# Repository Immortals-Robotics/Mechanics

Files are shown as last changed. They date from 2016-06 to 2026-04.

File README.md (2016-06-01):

# Immortals Mechanics
The mechanical design of robots has no major change since 2012 and just some part of kicking system and dribbling system optimized for better performance.
The main chassis consists of a **5mm hard anodized 7075 aluminum alloy** plate on which motors, batteries, encoders, capacitors, and kicker systems are mounted. Robots are covered by a **carbon-fiber compound** that is light as it is solid.
In order to mechanically stabilize the robot movement and kicking, the altitude of the center of mass is lowered by arranging rather heavy parts on the plate, that level first in the whole robot structure.
The overall height of the robot is **148mm** and its diameter is **178mm**.
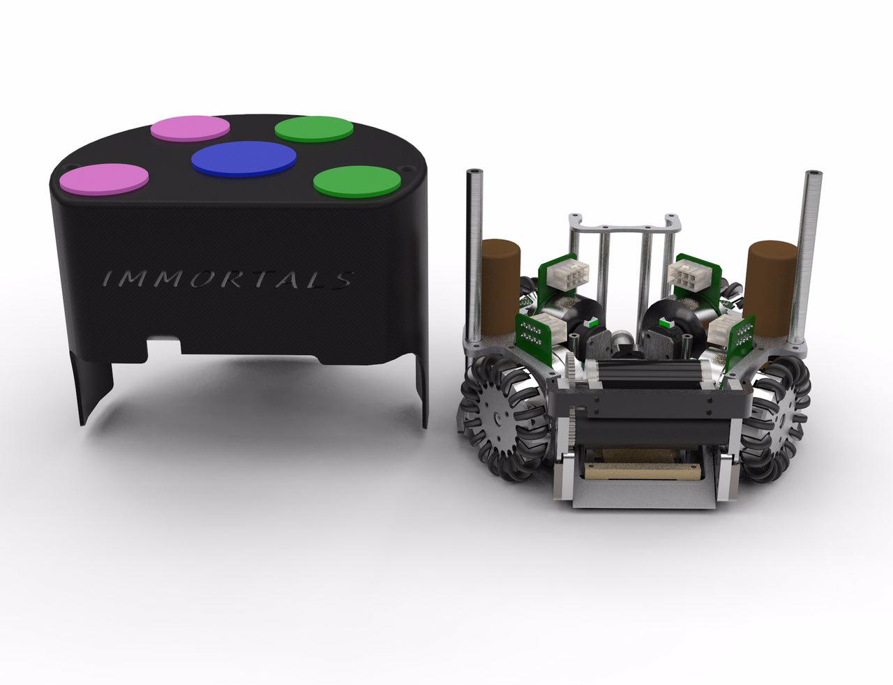
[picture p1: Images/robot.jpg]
Robot
 

## Wheels 
Robots are designed omni-directional by using **four** omni-wheels. Each wheel is **61mm** in diameters and has **18** rollers covered by double seal O-rings for better grip. Both wheels and rollers are made of **7075 aluminum alloy**. 
As the field size has been increased, higher speeds are inevitable; so the gear ratio is optimized to **45:12** and **50 Watts Maxon EC-45 brushless** motors are used to overcome the max-speed/max-acceleration trade off. The gearbox is merged into wheels to minimize the volume occupied by driving system. Its design is unique so that the gear used for transition is carved into the wheel itself.
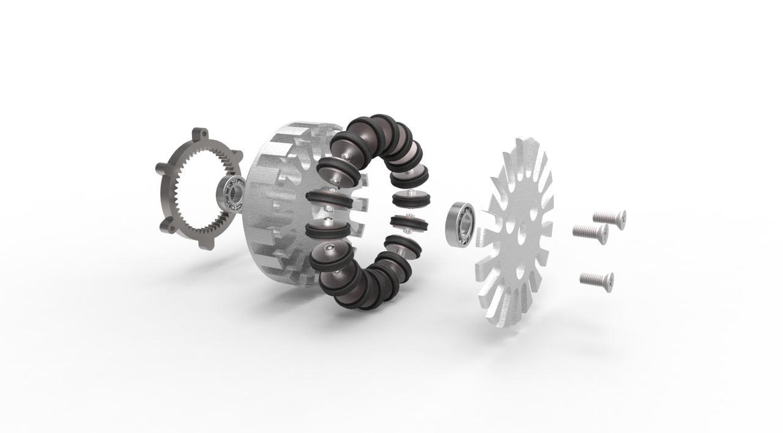
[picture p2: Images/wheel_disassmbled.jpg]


One of the major issues in the robots was inaccurate low-level navigation. After many experiments, measurements and inspections on the control system, it came out that non-identical mechanical properties of each gear are the biggest issue, which was caused by manufacturing inaccuracies. To have smoother and more accurate movement, gear module is redesigned with smaller module size this year. Also there are a little change in sub wheels design and tolerance to reduce unsteadiness and to stick better to the field during fast accelerations.   
## Casing
Although safe navigation has been a must for years in the league, highly dynamic nature of the SSL causes unavoidable collisions that lead to damages ranging from minor to severe. To avoid damages to internal parts, especially electronics which are fragile, making a robust, solid casing that can efficiently damp impacts is a necessity. Thus, a case made up of **2mm thick carbon-fiber compound** is made which is as solid as it is light to cover the whole body but kicking devices and the dribbler.

## Kicking & Dribbling System
To account for the increase in field size, the kicking system is redesigned and to have more power and accuracy in booth chip and direct shoots. Also because of some high voltage short circuit caused by magnet solenoids, in our new version whole kick system is isolated from body and there isn't any direct metal to metal contact by using resin as an isolator material. 
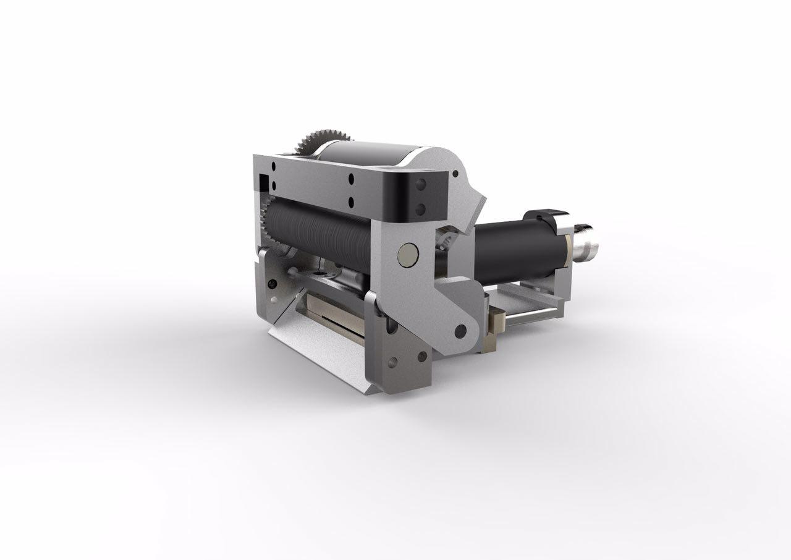
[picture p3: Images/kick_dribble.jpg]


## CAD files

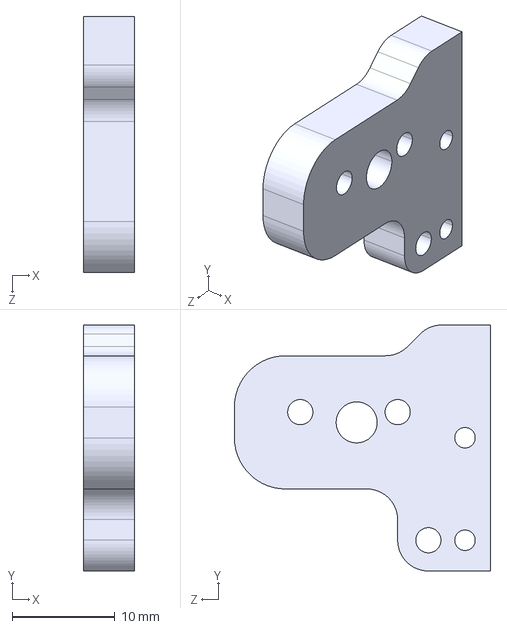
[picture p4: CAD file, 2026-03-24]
Manufacturing/Step/main holder (2 times).STEP
5.00 x 24.0 x 25.0 mm

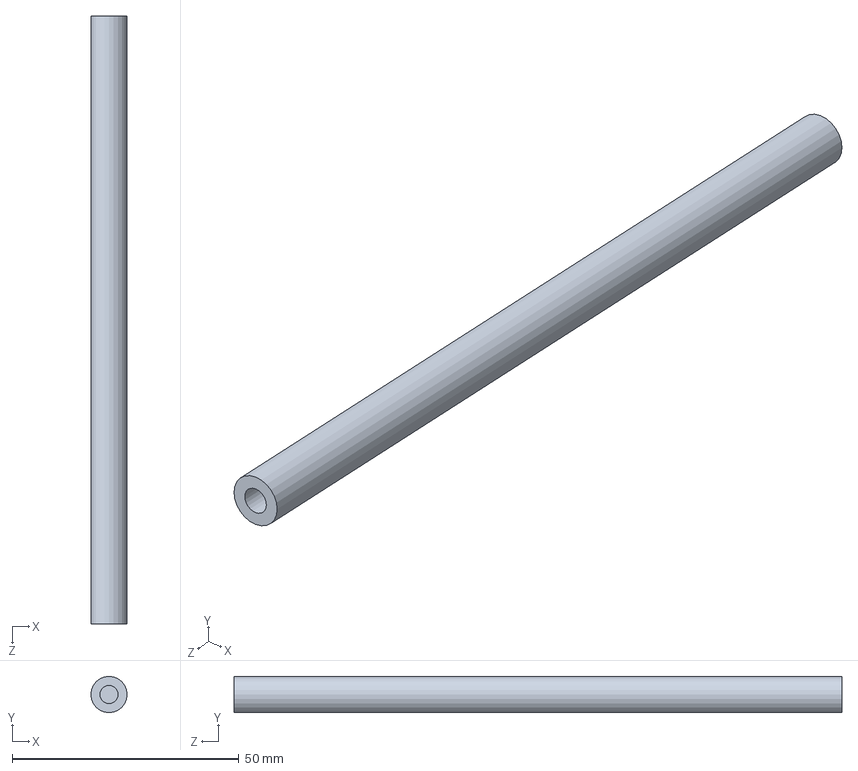
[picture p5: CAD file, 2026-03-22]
Spacer main.SLDPRT
8.00 x 8.00 x 134.0 mm

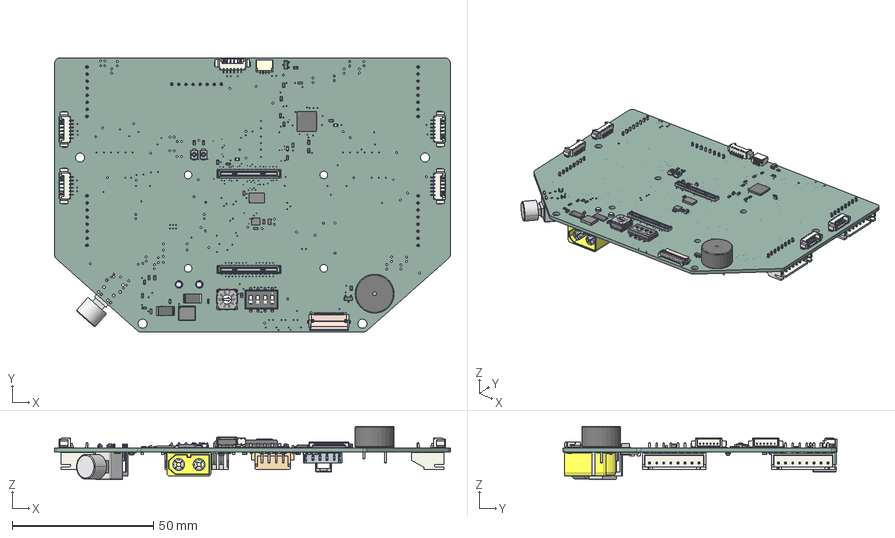
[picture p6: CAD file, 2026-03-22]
elec/main-board.step
140.0 x 97.0 x 18.9 mm
R_0603_1608Metric x 38
SOT-23 x 2
Indicator_PUI_AI-1440-TWT-24V-2-R
C_0603_1608Metric x 26
Molex_PicoBlade_53261-0671_1x06-1MP_P1.25mm_Horizontal x 5
FH12-22S-0.5SH_Èª
LED_0603_1608Metric x 3
ICM-42688-P
C_0805_2012Metric x 12
SW_DIP_SPSTx04_Slide_6.7x11.72mm_W8.61mm_P2.54mm_LowProfile
R_2512_6332Metric x 3
DHVQFN24
SW_SPST_B3U-1000P x 2
DF40C-100DS x 2
QFN-56-1EP_7x7mm_P0.4mm_EP3.2x3.2mm
BSC007N04LS6ATMA1
Nidec_Copal_SH-7010A
SH-700-Without knob (Minus slot)
SH-7050A_body
SM04B-SRSS-TB(LF)(SN)--3DModel-STEP-56544
JST_XH_S8B-XH-A_1x08_P2.50mm_Horizontal x 5
SOT-353_SC-70-5
TSOT-23-8
L_Bourns_SRN6045TA
CP_EIA-7343-31_Kemet-D
PB400OAQR1BLK_PB400OAQR1BLK
XT60PW-M--3DModel-STEP-269445
S4B-XH-SM4-TB_LF__SN_
main-board_PCB

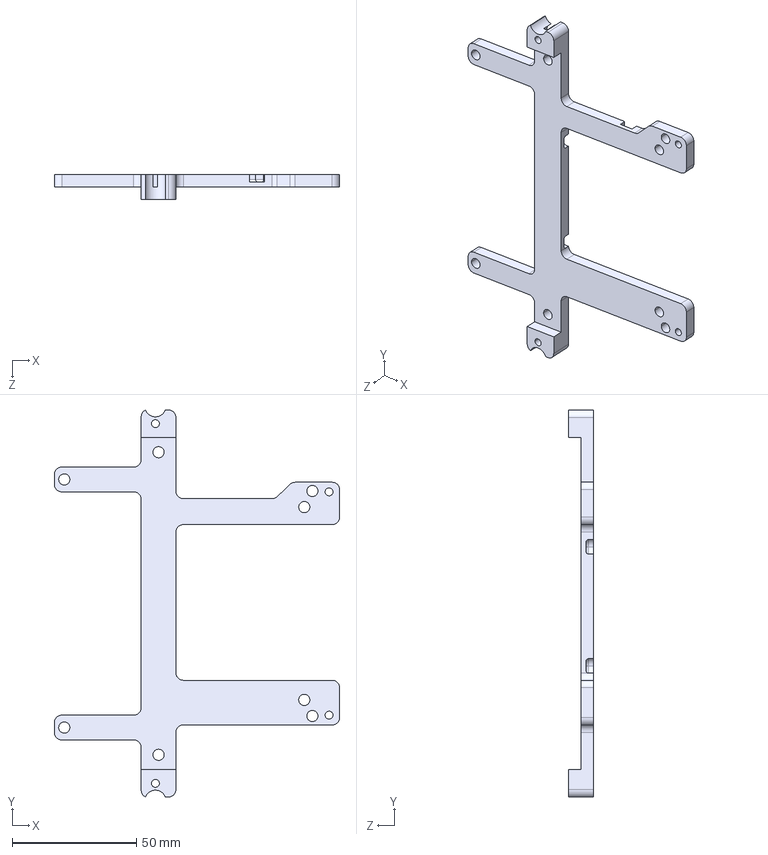
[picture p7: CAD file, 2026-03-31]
step/main board holder.STEP
115.0 x 156.0 x 10.0 mm

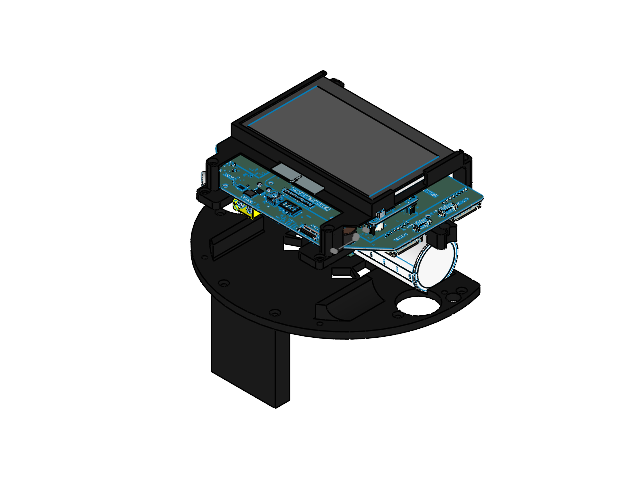
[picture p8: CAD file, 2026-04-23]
second floor asm.SLDASM
second floor
cap holder pcb
main board holder
main board asm
lcd
lcd holder
wifi antenna
SOLID_1.step x 3
COMPOUND_1.step x 3
COMPOUND-0_1.step x 2
SOLID-1.step
SOLID-2.step x 3
SOLID-3_1.step x 8
SOLID-4_1.step
SOLID-5.step
SOLID-6.step
SOLID-7.step x 17
SOLID-8_1.step
SOLID-9.step
SOLID-10_1.step
SOLID-11.step
SOLID-12_1.step x 5
SOLID-13.step
COMPOUND-14.step
SOLID-15.step
SOLID-16.step x 3
SOLID-17.step
SOLID-18.step x 2
COMPOUND-19.step
SOLID-20.step x 2
SOLID-21.step x 3
SOLID-22.step
SOLID-23.step
mikona PCB.step
mikona-holder-back

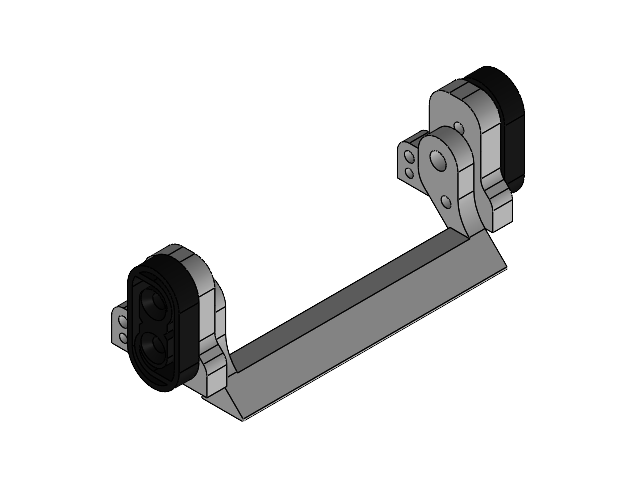
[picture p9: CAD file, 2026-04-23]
spin/holder-chip-damper.SLDASM
main holder x 2
chipper
damper-right
damper-left

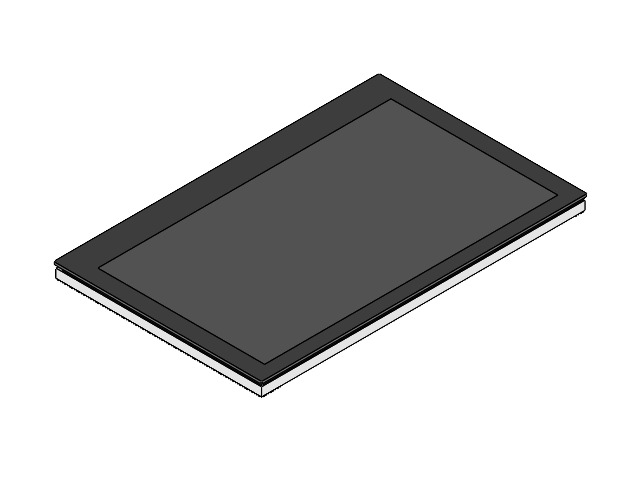
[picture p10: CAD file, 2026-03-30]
elec/lcd.SLDASM
43H-800480-IPS.stp
43H-800480-PCBA.stp
43H-800480-TP.stp
43H-TP-FILM.stp

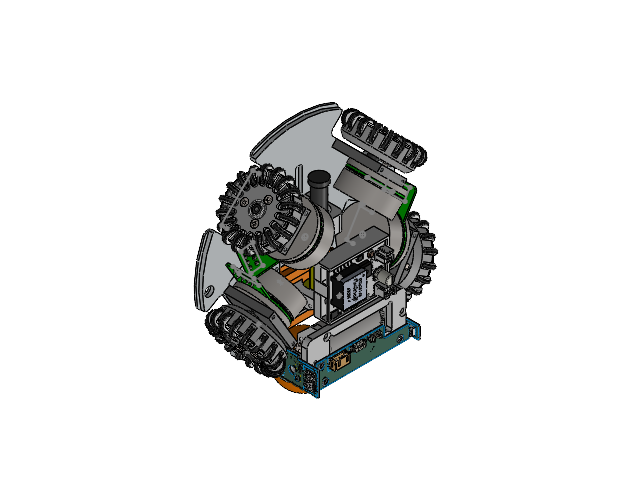
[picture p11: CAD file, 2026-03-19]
Mech-v2/plate-wheels-kick-asm-v2.SLDASM
plate-v2
paye 3
shaft 2 x 2
paye 1
EC-45 flat 50watt x 4
Metric - Spur gear 0.6M 12T 20PA 4FW ---S12N75H50L4.0N x 4
wheel hub x 4
wheel cover x 4
pin 3_6 para x 72
B18.6.7M - M3 x 0.5 x 8 Type I Cross Recessed FHMS --8S x 12
Metric - Internal spur gear 0.6M 49T 20PA 4FW ---S49S36OD 1.0AF x 4
subwheel x 72
90025k368 x 72
paye 4
shaft 1 x 2
bracket
ISO - Spur gear 0.5M 20T 20PA 5FW ---S20B75H10L4.0N
ISO 15 RBB - 273 - 12,SI,NC,12_68
ISO - Spur gear 0.5M 20T 20PA 5FW ---S20B75H10L6.0N x 2
ISO 15 RBB - 276 - 16,SI,NC,16_68 x 2
slider - left
spinner
holder motor
IR-sensor-top
IR-sensor-left
IR-sensor-right
slider - right
tube
MaxonECmax22-25W
flat magnet
Golfball.ipt
main holder x 2
chipper
damper-right
damper-left
paye 2
Kick front holder
kick solenoid
kick back holder
core 1
kicker
ISO 14581 M4x10x10-N
ISO 14581 M3x5x5-N
mikona holder
SOLID_1.step x 3
COMPOUND_1.step x 3
COMPOUND-0_1.step x 2
SOLID-1.step
SOLID-2.step x 3
SOLID-3_1.step x 8
SOLID-4_1.step
SOLID-5.step
SOLID-6.step
SOLID-7.step x 17
SOLID-8_1.step
SOLID-9.step
SOLID-10_1.step
SOLID-11.step
SOLID-12_1.step x 5
SOLID-13.step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

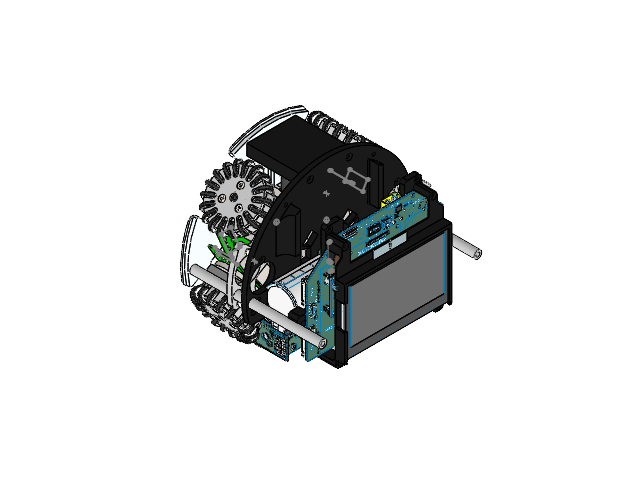
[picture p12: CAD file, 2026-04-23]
Robot.SLDASM
plate-v2
wheel hub x 4
wheel cover x 4
pin 3_6 para x 72
B18.6.7M - M3 x 0.5 x 8 Type I Cross Recessed FHMS --8S x 12
Metric - Internal spur gear 0.6M 49T 20PA 4FW ---S49S36OD 1.0AF x 4
subwheel x 72
90025k368 x 72
EC-45 flat 50watt x 4
Metric - Spur gear 0.6M 12T 20PA 4FW ---S12N75H50L4.0N x 4
motor holder back x 2
shaft 1 x 4
motor holder front x 2
main holder x 2
chipper
damper-right
damper-left
bracket
ISO - Spur gear 0.5M 20T 20PA 5FW ---S20B75H10L4.0N
ISO 15 RBB - 273 - 12,SI,NC,12_68
ISO - Spur gear 0.5M 20T 20PA 5FW ---S20B75H10L6.0N x 2
ISO 15 RBB - 276 - 16,SI,NC,16_68 x 2
slider - left
spinner
holder motor
IR-sensor-top
IR-sensor-left
IR-sensor-right
slider - right
tube
MaxonECmax22-25W
flat core
flat magnet
kick back holder
Kick front holder
kick solenoid
core 1
kicker
second floor
cap holder pcb
main board holder
main board asm
lcd
lcd holder
wifi antenna
SOLID_1.step x 3
COMPOUND_1.step x 3
COMPOUND-0_1.step x 2
SOLID-1.step
SOLID-2.step x 3
SOLID-3_1.step x 8
SOLID-4_1.step
SOLID-5.step
SOLID-6.step
SOLID-7.step x 17
SOLID-8_1.step
SOLID-9.step
SOLID-10_1.step
SOLID-11.step
SOLID-12_1.step x 5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

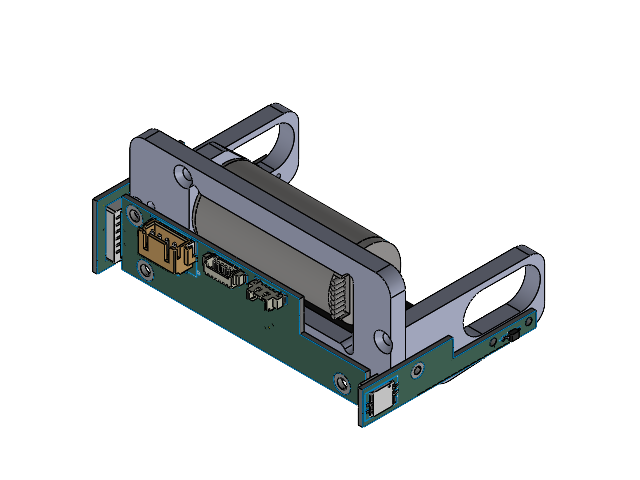
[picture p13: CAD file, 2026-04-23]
spin/spin.SLDASM
bracket
ISO - Spur gear 0.5M 20T 20PA 5FW ---S20B75H10L4.0N
ISO 15 RBB - 273 - 12,SI,NC,12_68
ISO - Spur gear 0.5M 20T 20PA 5FW ---S20B75H10L6.0N x 2
ISO 15 RBB - 276 - 16,SI,NC,16_68 x 2
slider - left
spinner
holder motor
IR-sensor-top
IR-sensor-left
IR-sensor-right
slider - right
tube
MaxonECmax22-25W

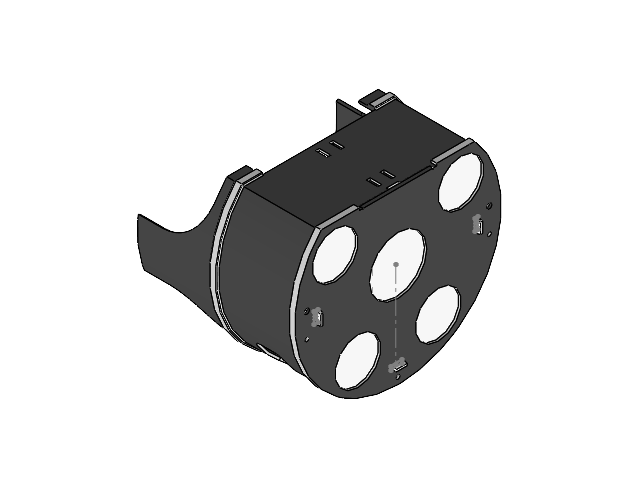
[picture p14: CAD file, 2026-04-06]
cover asm.SLDASM
Cover
blob-cover

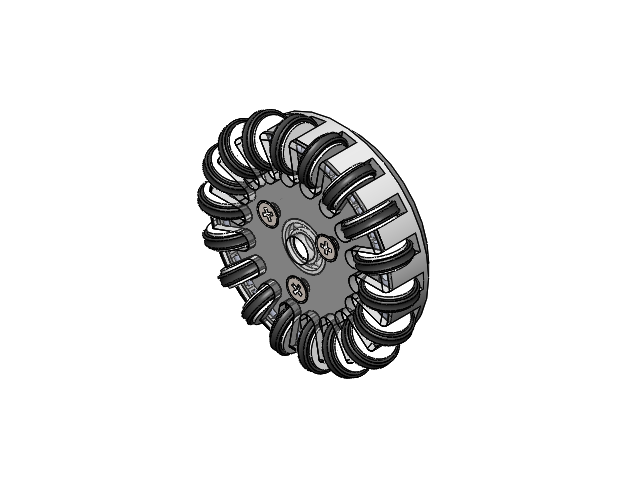
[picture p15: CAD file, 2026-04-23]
Drive system/Assem wheel.SLDASM
wheel hub
wheel cover
pin 3_6 para x 18
B18.6.7M - M3 x 0.5 x 8 Type I Cross Recessed FHMS --8S x 3
Metric - Internal spur gear 0.6M 49T 20PA 4FW ---S49S36OD 1.0AF
subwheel x 18
90025k368 x 18

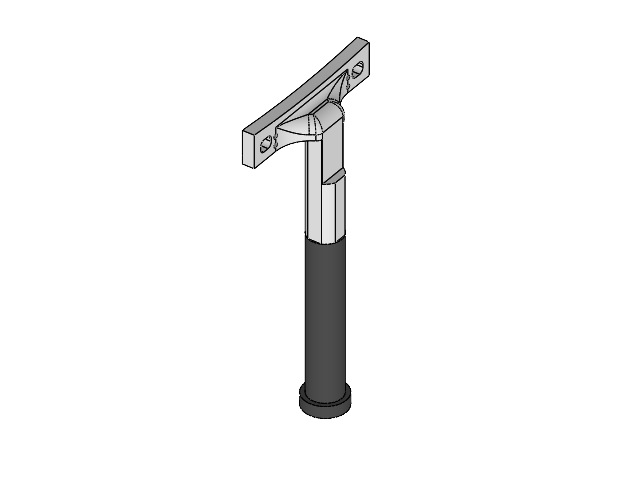
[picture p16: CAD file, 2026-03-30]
kick/kicker asm.SLDASM
core 1
kicker

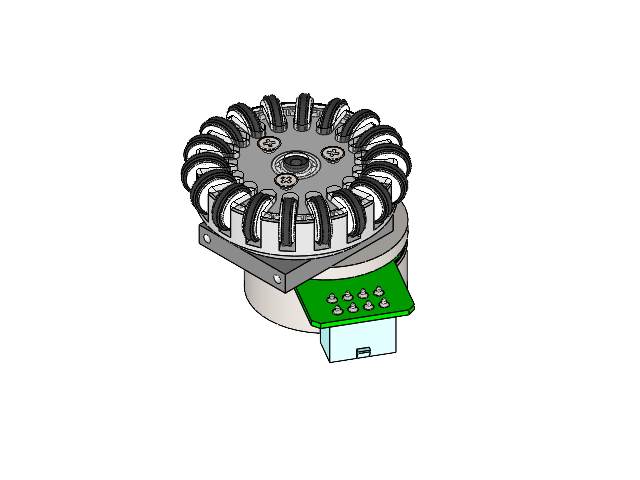
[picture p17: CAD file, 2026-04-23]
Drive system/motor back 1 asm.SLDASM
wheel hub
wheel cover
pin 3_6 para x 18
B18.6.7M - M3 x 0.5 x 8 Type I Cross Recessed FHMS --8S x 3
Metric - Internal spur gear 0.6M 49T 20PA 4FW ---S49S36OD 1.0AF
subwheel x 18
90025k368 x 18
EC-45 flat 50watt
Metric - Spur gear 0.6M 12T 20PA 4FW ---S12N75H50L4.0N
motor holder back
shaft 1

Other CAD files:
elec/main board asm.SLDASM
kick/mikona.SLDASM
Drive system/motor front asm.SLDASM
spin/step/main holder.STEP
2D/bracket.SLDDRW
2D/chipper.SLDDRW
2D/holder motor.SLDDRW
2D/main holder.SLDDRW
2D/plate-v2.SLDDRW
2D/rail.SLDDRW
2D/slider - left.SLDDRW
2D/slider - right.SLDDRW
2D/spinner.SLDDRW
2D/top motor holder.SLDDRW
3mf/Color changer.3mf
3mf/cover.3mf
3mf/main board holder.3mf
3mf/motor-magnet-holder.3mf
3mf/second floor.3mf
Color changer.SLDPRT
Cover.SLDPRT
Drive system/618_6.SLDPRT
Drive system/90025k368.SLDPRT
Drive system/Assem subwheel.SLDASM
Drive system/EC-45 flat 50watt with gear.SLDPRT.SLDASM
Drive system/EC-45 flat 50watt.SLDPRT
Drive system/motor back 2 asm.SLDASM
Drive system/motor holder back.SLDPRT
Drive system/motor holder front.SLDPRT
Drive system/pin 3_6 para.SLDPRT
Drive system/shaft 1.SLDPRT
Drive system/subwheel.SLDPRT
Drive system/wheel cover.SLDPRT
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

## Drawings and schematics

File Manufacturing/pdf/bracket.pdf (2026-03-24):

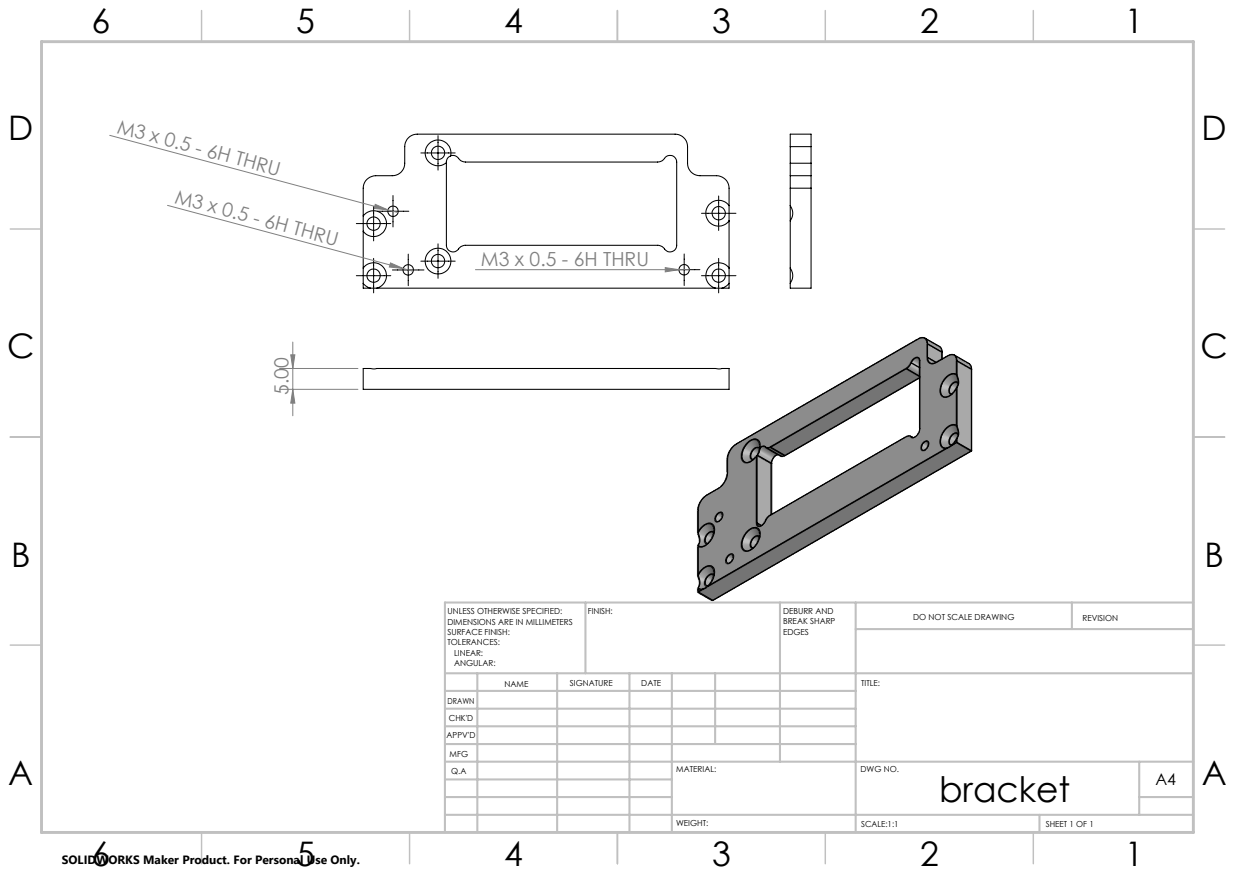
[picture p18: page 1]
M3 x 0.5 - 6H THRU; FINISH:; DEBURR AND; BREAK SHARP; DO NOT SCALE DRAWING; REVISION; SCALE:1:1; SHEET 1 OF 1

UNLESS OTHERWISE SPECIFIED:
DIMENSIONS ARE IN MILLIMETERS
SURFACE FINISH:
TOLERANCES:
LINEAR:
ANGULAR:

NAME | SIGNATURE | DATE | | | | TITLE:

DRAWN
CHK'D
APPV'D
MFG
Q.A | | | | MATERIAL: | DWG NO. bracket | A4

SOLIDWORKS Maker Product. For Personal Use Only.

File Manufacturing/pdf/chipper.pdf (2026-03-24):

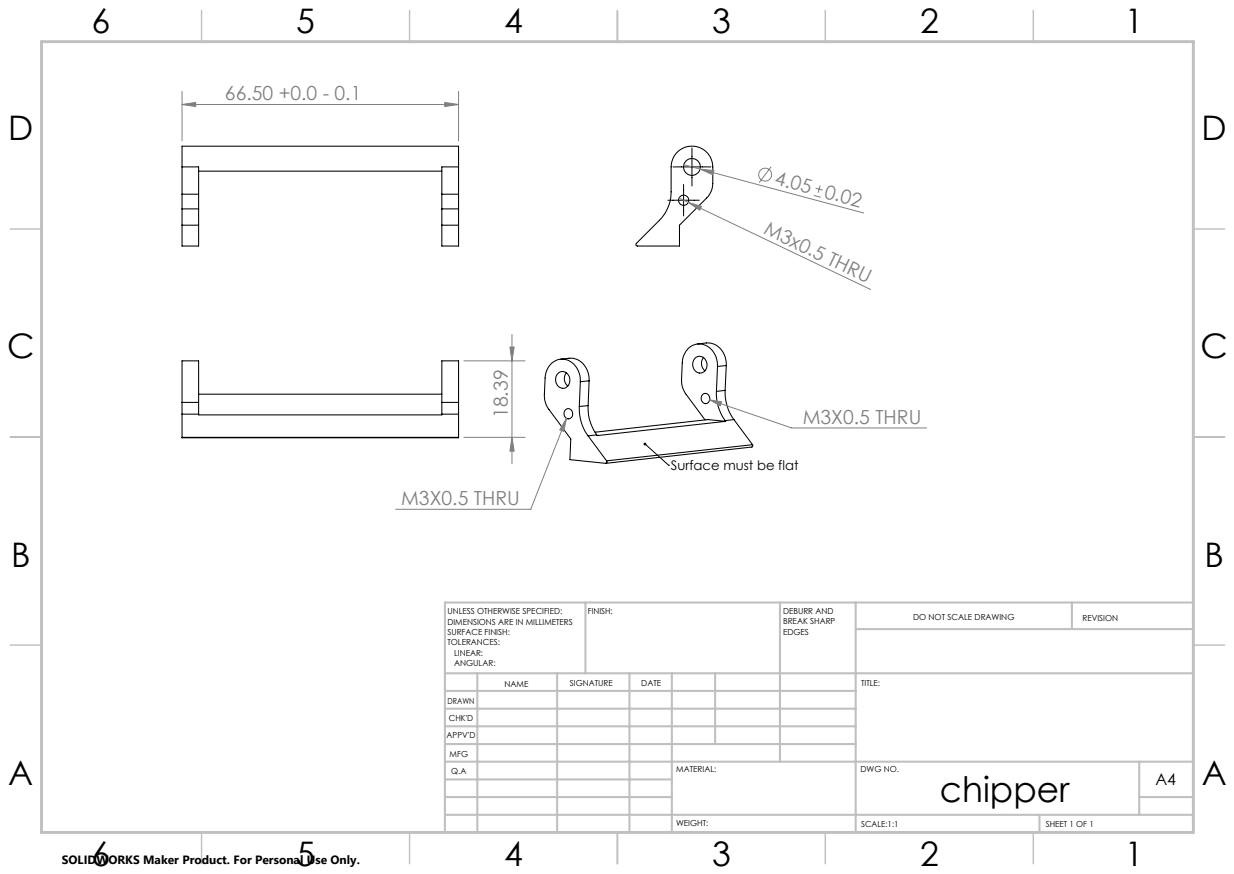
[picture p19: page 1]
M3x0.5 THRU; M3X0.5 THRU; FINISH:; DEBURR AND; BREAK SHARP; DO NOT SCALE DRAWING; REVISION; SCALE:1:1; SHEET 1 OF 1

Surface must be flat

UNLESS OTHERWISE SPECIFIED:
DIMENSIONS ARE IN MILLIMETERS
SURFACE FINISH:
TOLERANCES:
LINEAR:
ANGULAR:

NAME | SIGNATURE | DATE | | | | TITLE:

DRAWN
CHK'D
APPV'D
MFG
Q.A | | | | MATERIAL: | DWG NO. chipper | A4

SOLIDWORKS Maker Product. For Personal Use Only.

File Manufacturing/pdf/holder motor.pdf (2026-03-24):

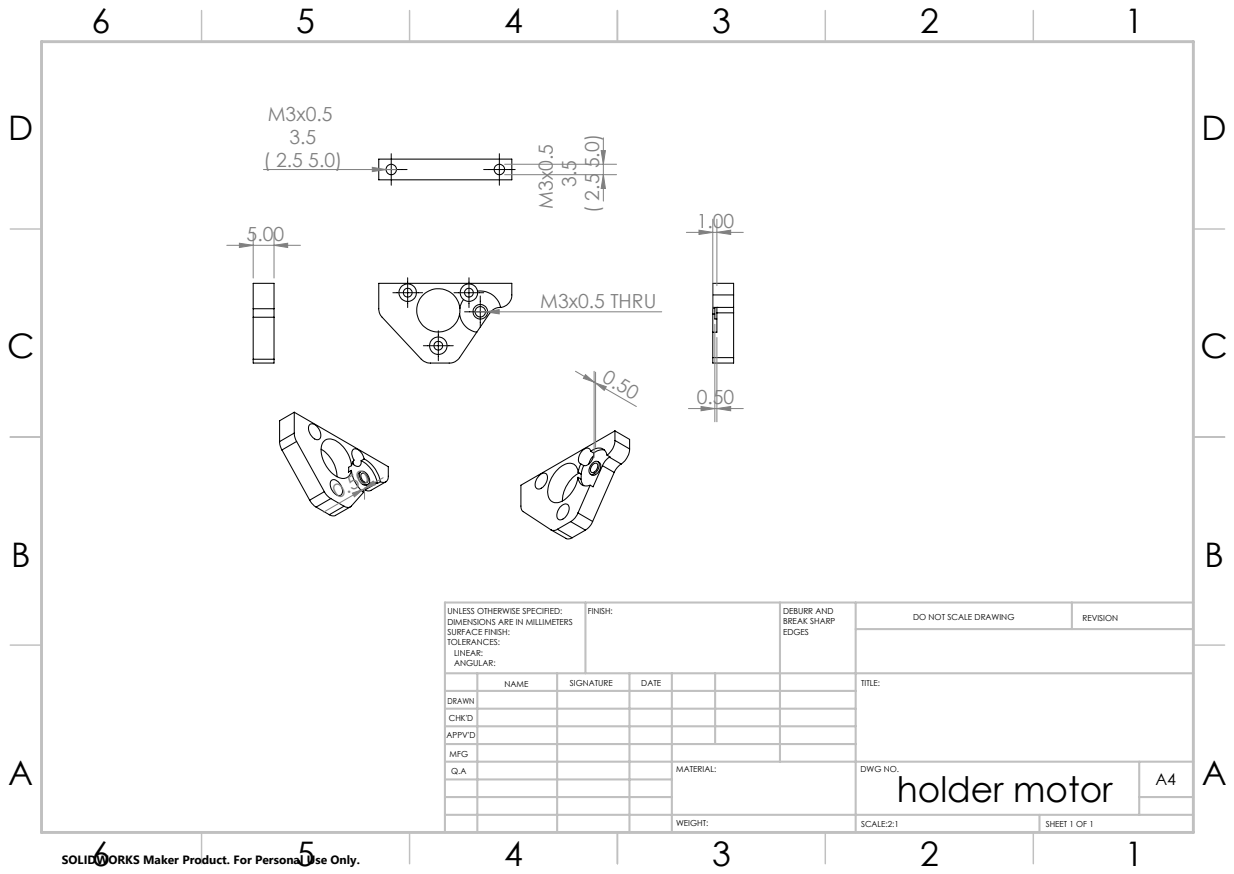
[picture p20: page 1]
M3x0.5 THRU; FINISH:; DEBURR AND; BREAK SHARP; DO NOT SCALE DRAWING; REVISION; SCALE:2:1; SHEET 1 OF 1

UNLESS OTHERWISE SPECIFIED:
DIMENSIONS ARE IN MILLIMETERS
SURFACE FINISH:
TOLERANCES:
LINEAR:
ANGULAR:

NAME | SIGNATURE | DATE | | | | TITLE:

DRAWN
CHK'D
APPV'D
MFG
Q.A | | | | MATERIAL: | DWG NO. holder motor | A4

SOLIDWORKS Maker Product. For Personal Use Only.

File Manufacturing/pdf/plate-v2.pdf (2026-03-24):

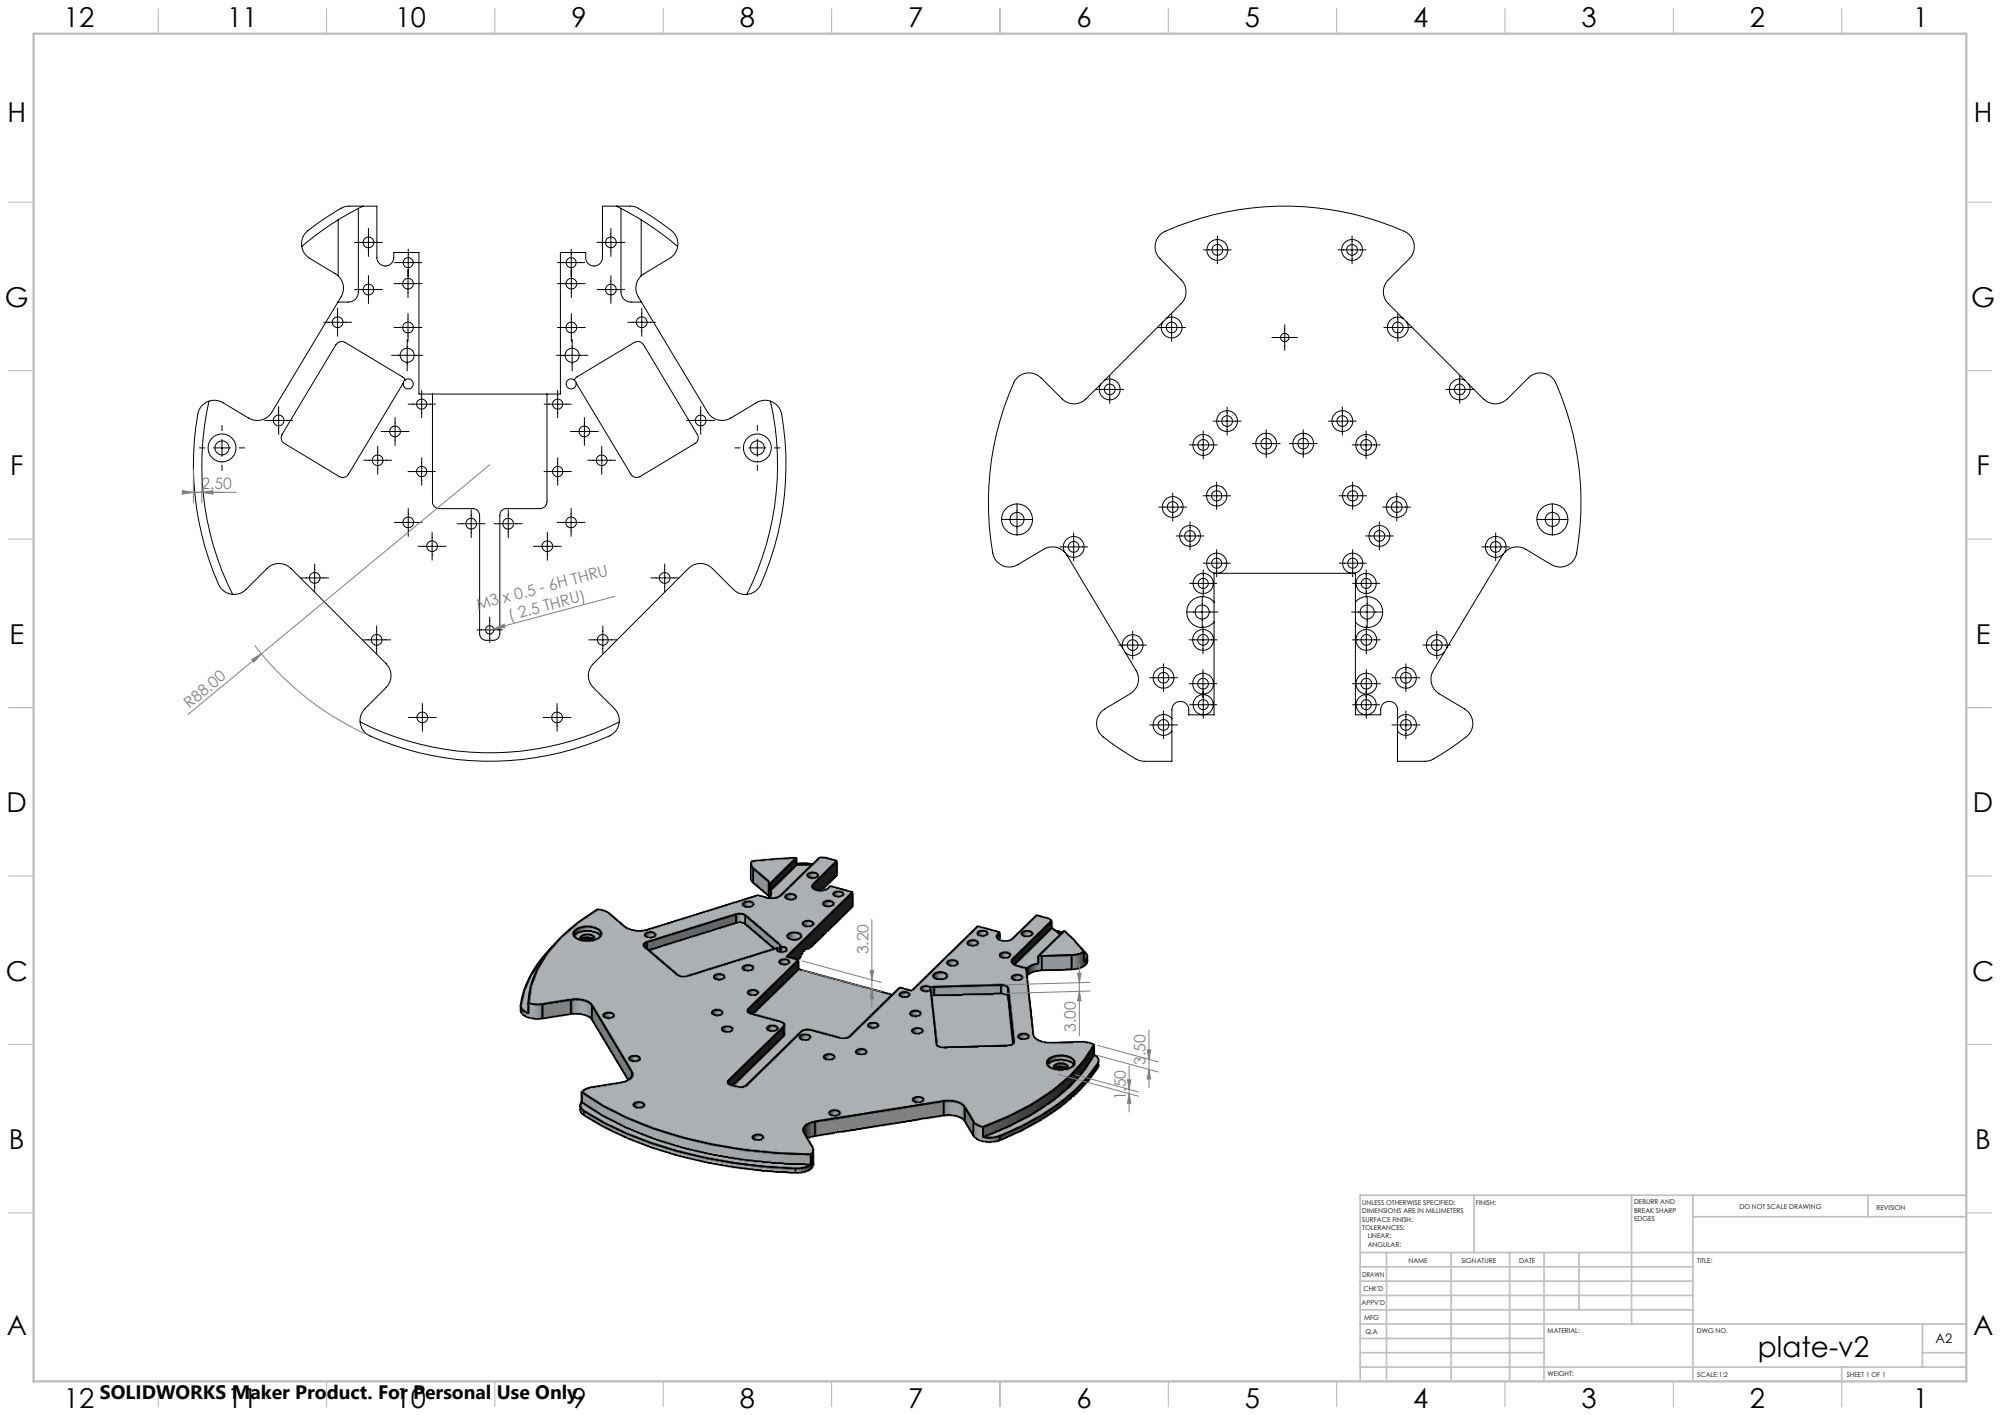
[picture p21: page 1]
M3 x 0.5 - 6H THRU ( 2.5 THRU); FINISH:; DEBURR AND; BREAK SHARP; DO NOT SCALE DRAWING; REVISION; SCALE:1:2; SHEET 1 OF 1

UNLESS OTHERWISE SPECIFIED:
DIMENSIONS ARE IN MILLIMETERS
SURFACE FINISH:
TOLERANCES:
LINEAR:
ANGULAR:

NAME | SIGNATURE | DATE | | | | TITLE:

DRAWN
CHK'D
APPV'D
MFG
Q.A | | | | MATERIAL: | DWG NO. plate-v2 | A2

SOLIDWORKS Maker Product. For Personal Use Only.

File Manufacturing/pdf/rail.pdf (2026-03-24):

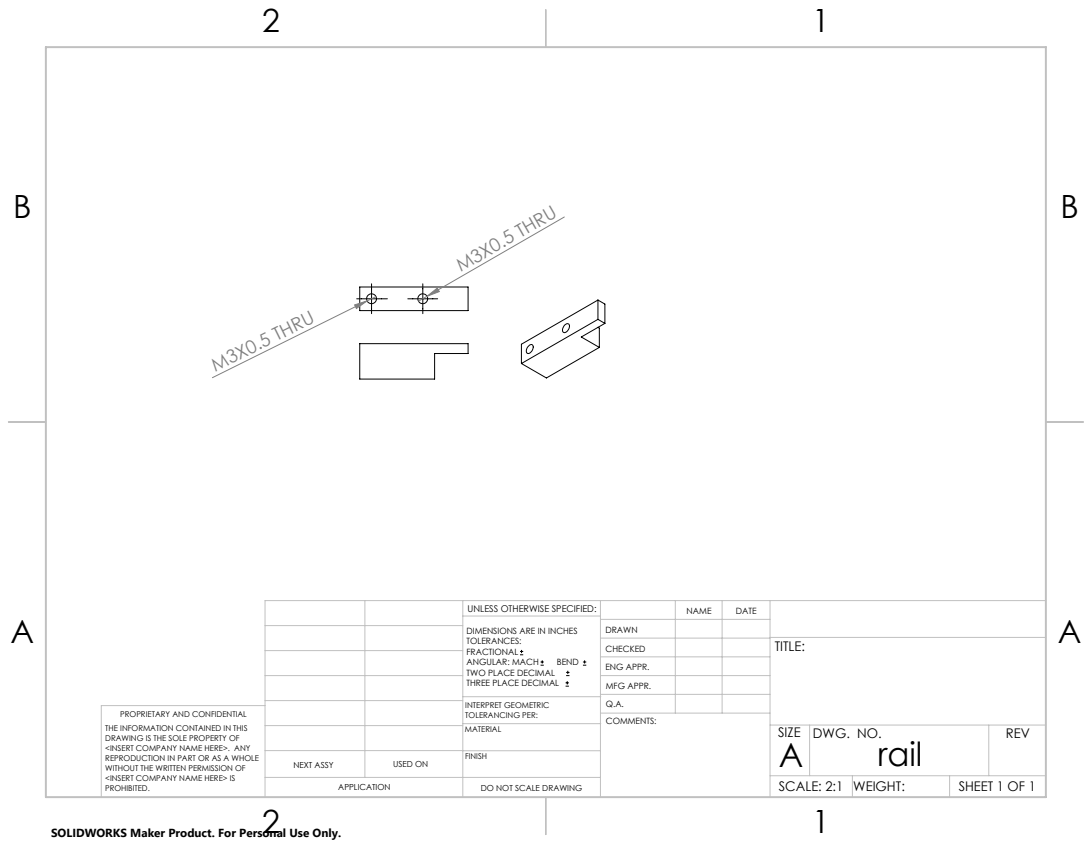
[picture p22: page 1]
M3X0.5 THRU

UNLESS OTHERWISE SPECIFIED: | | NAME | DATE
DIMENSIONS ARE IN INCHES TOLERANCES: FRACTIONAL ANGULAR: MACH BEND TWO PLACE DECIMAL THREE PLACE DECIMAL | DRAWN

CHECKED | | | TITLE:

ENG APPR.
MFG APPR.

INTERPRET GEOMETRIC TOLERANCING PER: | Q.A.
MATERIAL | | SIZE A | DWG. NO. rail | REV

PROPRIETARY AND CONFIDENTIAL
THE INFORMATION CONTAINED IN THIS
DRAWING IS THE SOLE PROPERTY OF
<INSERT COMPANY NAME HERE>. ANY
REPRODUCTION IN PART OR AS A WHOLE
WITHOUT THE WRITTEN PERMISSION OF
<INSERT COMPANY NAME HERE> IS
PROHIBITED.

NEXT ASSY | USED ON | FINISH

APPLICATION | DO NOT SCALE DRAWING | | SCALE: 2:1 | WEIGHT: | SHEET 1 OF 1

SOLIDWORKS Maker Product. For Personal Use Only.

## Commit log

2016-05-03 Initial submission
    [618_6.SLDPRT, 90025k368.SLDPRT, Assem subwheel.SLDASM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]
2016-05-03 Moved everything to Solidworks folder
    [618_6.SLDPRT, 90025k368.SLDPRT, Assem subwheel.SLDASM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]
2016-06-01 Added cad drawings, and images.
2025-08-04 Move old mechanics into Mech V1
    [618_6.SLDPRT, 90025k368.SLDPRT, Assem subwheel.SLDASM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]
2025-08-04 Mech V2 First commit
    [IR-sensor-left.SLDPRT, IR-sensor-right.SLDPRT, IR-sensor-top.SLDPRT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]
2026-03-19 surakh ha
    [plate-v2.SLDPRT]
2026-03-19 update main plate + mikona holder + old kick
    [IR-sensor-left.SLDPRT, IR-sensor-right.SLDPRT, IR-sensor-top.SLDPRT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]
2026-03-22 Add pcbs
    [main board asm.SLDASM, main-board.SLDASM, main-board.step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]
2026-03-22 make top bracket smaller for better movement
    [bracket.SLDPRT, spin.SLDASM]
2026-03-22 cap holder + battery
    [Spacer mikona.SLDPRT, Spacer.SLDPRT, battery holder.SLDPRT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]
2026-03-24 Finalize drawings for cnc
    [bracket.SLDDRW, bracket.STEP, chipper.SLDDRW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]
2026-03-26 cap holder pcb + mikona holder back
    [Part1.SLDPRT, battery holder.STEP, cap holder pcb.SLDPRT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]
2026-03-29 new cap holder + pcb holder + cover
    [Cover.SLDPRT, battery holder.SLDPRT, cap holder pcb.SLDPRT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]
2026-03-29 cover and color changer
    [Color changer.SLDPRT, Color changer.STEP, Cover.SLDPRT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]
2026-03-30 lcd holder
    [Color changer.SLDPRT, Color changer.STEP, kicker asm.SLDASM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]
2026-03-31 wifi antena + cm4 spacer + sub wheel press
    [cm4 spacer.SLDPRT, cm4 spacer.STEP, lcd holder.SLDPRT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]
2026-03-31 update cover and lcd holder
    [Cover.SLDPRT, cover.STEP, lcd holder.SLDPRT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]
2026-04-03 Update Color changer
    [Color changer.SLDPRT, Color changer.STEP, case-cm4-nano.stl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]
2026-04-03 3mf file for color changer
    [Color changer.3mf]
2026-04-03 create 3mf folder
    [Color changer.3mf, main board holder.3mf]
2026-04-03 second floor 3mf
    [second floor.3mf]
2026-04-03 cover 3mf
    [cover.3mf]
2026-04-06 New settings for cover
    [cover.3mf]
2026-04-06 IR sensor covers
    [cover-ir-rx.SLDPRT, cover-ir-rx.STEP, cover-ir-tx.SLDPRT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]
2026-04-06 Blob cover
    [blob-cover.SLDPRT, blob-cover.STEP]
2026-04-06 Add blob and IR covers to ASM files
    [cover asm.SLDASM, second floor asm.SLDASM]
2026-04-06 Update IR cover and make them a bit bigger
    [cover-ir-rx.SLDPRT, cover-ir-rx.STEP, cover-ir-tx.SLDPRT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]
2026-04-07 Add damper v1 and update second floor
    [damper-1.SLDPRT, damper-1.STEP, second floor asm.SLDASM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]
2026-04-07 damper on paye
    [damper-1-kick-holder.SLDPRT, damper-1-kick-holder.STEP]
2026-04-07 bottom damper
    [bottom damper.SLDPRT, bottom damper.STEP]
2026-04-08 Add a temporary hack for chipper's spring anchor.
    [chipper-spring-anchor.stl]
2026-04-08 motor magnet no support + new bottom damper
    [bottom damper-mirror.SLDPRT, bottom damper-mirror.STEP, bottom damper.SLDPRT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]
2026-04-08 motor holder 3mf
    [motor-magnet-holder.3mf]
2026-04-08 damper left right + 0.5mm
    [damper-left.SLDPRT, damper-left.STEP, damper-right.SLDPRT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]
2026-04-10 update magnet holder
    [motor-magnet-holder.SLDPRT, motor-magnet-holder.STEP]
2026-04-11 Revert "Add a temporary hack for chipper's spring anchor."
    This reverts commit 5a3f7ed6f8f8f70c5e5852abf4547ae47a523d14.
    [chipper-spring-anchor.stl]
2026-04-11 secon floor gap
    [holder-chip-damper.SLDASM, second floor asm.SLDASM, second floor-flat.STEP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]
2026-04-16 Flat rail.
    [rail.SLDPRT]
2026-04-23 Reorganize files + fix asm problems + fix plate v2 spin holes
    [618_6.SLDPRT, 90025k368.SLDPRT, Assem subwheel.SLDASM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]
